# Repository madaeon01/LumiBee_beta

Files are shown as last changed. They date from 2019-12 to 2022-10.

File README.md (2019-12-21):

# LumiBee_beta

This is a WIP project.
Here you can find:
-all the 3d printable parts as STL;
-all the non 3d printable parts;
-the PCB eagle files;
-the arduino firmware;
-the chitubox profiles;
-the Android APP beta. Note: the current app stores the PNGs in the app directly, so you must put all your layers in the
RES\drawables folder manually, then compile. I plan to implement the ability to select files from a folder 
from the App, but at the moment, all the LumiBee development (hardware, software, firmware, app and all the testing) is done by 
ONE single person (me) as a side project, for free. So feel free to contribute.

To do:
-complete BOM
-assembly instructions
-how to use the screen luminosity tester
-how to use - guide
-how to use the app
In the next days this guide wil be update so if you do not find some info, just write me.

A 3D viewable model of the assembly is available here:
https://sketchfab.com/3d-models/lumibee-43fde758bdf04565baee1a75a64f292f

You can contribute to this project with a donation to support it if you like it, with a paypal donation at madaeon@gmail.com

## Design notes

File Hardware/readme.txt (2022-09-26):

List of hardware components.
Update: added latest STEP cad files.

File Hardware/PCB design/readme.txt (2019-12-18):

This is the last revision of the PCB design.

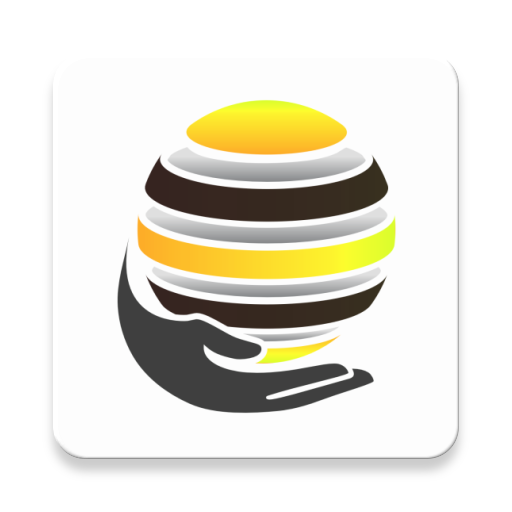
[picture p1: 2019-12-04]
app/src/main/ic_launcher-web.png

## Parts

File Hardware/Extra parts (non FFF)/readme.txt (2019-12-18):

Here you can find the parts that are not 3d printable.

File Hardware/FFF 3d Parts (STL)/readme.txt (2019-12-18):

Here you can find all the FFF printable files.

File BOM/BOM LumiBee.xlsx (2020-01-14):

Group | Part name | Printing order | Quantity | Infill | Material | Notes | Cost | Supplier
FFM Printed parts - black | LumiBee Segment A | plate 1 black | 1 | 30-40% | FDM Pla/Abs |  | n.d.
 | LumiBee Segment C | plate 1 black | 1 | 30-40% | FDM Pla/Abs |  | n.d.
 | LumiBee RoundFit conn | plate 1 black | 2+1 | 30-40% | FDM Pla/Abs |  | n.d.
 | LumiBee Segment E | plate 1 black | 1 | 30-40% | FDM Pla/Abs |  | n.d.
 | LumiBee tray PtA | plate 1 black | 1 | 70% ++ | FDM Pla/Abs |  | n.d.
 | LumiBee PostButton | plate 1 black | 3+1 | 30-40% | FDM Pla/Abs |  | n.d.
FFM Printed parts - yellow | LumiBee Segment B | plate 2 yellow | 1 | 30-40% | FDM Pla/Abs |  | n.d.
 | LumiBee Segment F | plate 2 yellow | 1 | 30-40% | FDM Pla/Abs |  | n.d.
 | LumiBee SnapFit conn | plate 2 yellow | 3+1 | 30-40% | FDM Pla/Abs |  | n.d.
 | LumiBee Round conn | plate 2 yellow | 2+1 | 30-40% | FDM Pla/Abs |  | n.d.
 | LumiBee Segment D | plate 2 yellow | 4 | 30-40% | FDM Pla/Abs |  | n.d.
 | LumiBee Leadscrew | plate 2 yellow | 2 | 70% ++ | FDM Pla/Abs |  | n.d.
 | LumiBee tray PtB | plate 2 yellow | 1 | 70% ++ | FDM Pla/Abs |  | n.d.
 | LumiBee Segment F Top Lid | plate 2 yellow | 1 | 30-40% | FDM Pla/Abs |  | n.d.
Hard plastic parts | Resin_Container |  | 1 |  | Resin 3d Printed | Can be machined from 14mm plexi too | n.d.
Neoprene parts | Neoprene-Border |  | 1 |  | Rigid 2mm Neoprene |  | n.d.
Aluminum laser cut parts | bottom-vat |  | 1 |  | Aluminium 4mm | CNC cut | n.d.
 | LumiBee Tray ALU plate |  | 1 |  | Aluminium 4mm | CNC cut | n.d.
Hardware | countersunk screw m3x6mm |  | 22 |  |  | 8 for bottom vat
 |  |  |  |  |  | 6 for LumiBee SnapFit conn
 |  |  |  |  |  | 4 for LumiBee Round conn
 |  |  |  |  |  | 4 for attaching vat to segment B
 |  |  |  |  |  | 4 for stepper motors
 | countersunk screw m3x8mm |  | 8 |  |  | 4 for alu plate
 |  |  |  |  |  | 4 for tray pt B
 | countersunk screw m3x16mm |  | 8 |  |  | 4 rear conn segment C
 |  |  |  |  |  | 4 attach segment C to parts of D
 | threaded insert M3x4mm |  | 12 |  |  | 4 for vat
 |  |  |  |  |  | 8 for segment D parts
 |  |  |  |  |  | 2 for top pcb on segment E
 | m3x8 screw |  | 4 |  |  | for endstops
 | m3x40 screw |  | 4 |  |  | for segment F
 | countersunk screw m3x13mm |  | 4 |  |  | for top fan
 | 4 m2x14 screws + nut |  | 4 |  |  | to hold leadscrews
 | Lm4uu linear bearing |  | 2
 | Linear shaft dia 4mm L=95mm |  | 2
 | Spacer nylon black M3 L=20mm |  | 4
Electronic components | Optical endstop |  | 2 |  |  | the led of the endstop must be removed and/or mounted on the other side of the pcb
 | Fan 12V 40x40x10mm |  | 1
 | Motech stepper 14 HR 05 |  | 2
 | LumiBee DC jack |  | 1
 | LumiBee PCB board |  | 1
 | stepstick 2130 |  | 2
 | arduino micro |  | 1
Plexiglass parts | LumiBee Side Plexi window |  | 2 |  | trasparent red plexiglass 3mm | Product name: "Metacrilato ACRIDITE 320 Rosso 1" |  | www.Plexishop.it
 | LumiBee Door Plexi |  | 2 |  | trasparent red plexiglass 3mm | Product name: "Metacrilato ACRIDITE 320 Rosso 1"
 | LumiBee Frame Plexi window |  | 2 |  | trasparent red plexiglass 3mm | Product name: "Metacrilato ACRIDITE 320 Rosso 1"
Magnets | Neodimium Cube 4x4x4mm |  | 8 |  |  |  |  | https://www.supermagnete.it/
 | Neodimium 5 x 2,5 x 2 mm Q-05-2.5-02-HN |  | 8

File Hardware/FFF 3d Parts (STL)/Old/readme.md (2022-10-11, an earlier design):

These parts are from a previous version, created in 2019 or earlier.

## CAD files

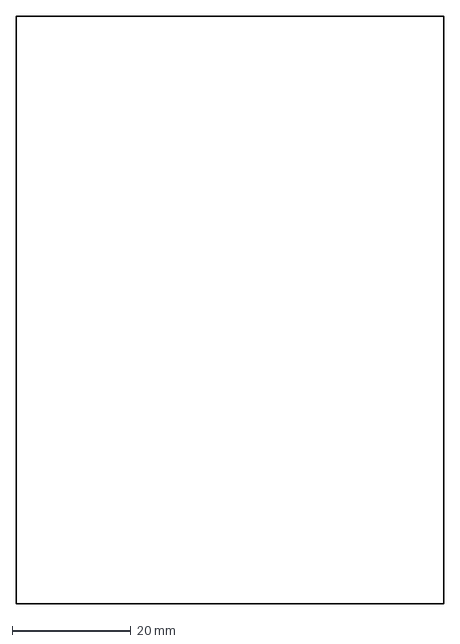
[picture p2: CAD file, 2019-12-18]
Hardware/Extra parts (non FFF)/LumiBee Side Plexi window.DXF
72.0 x 99.0 mm

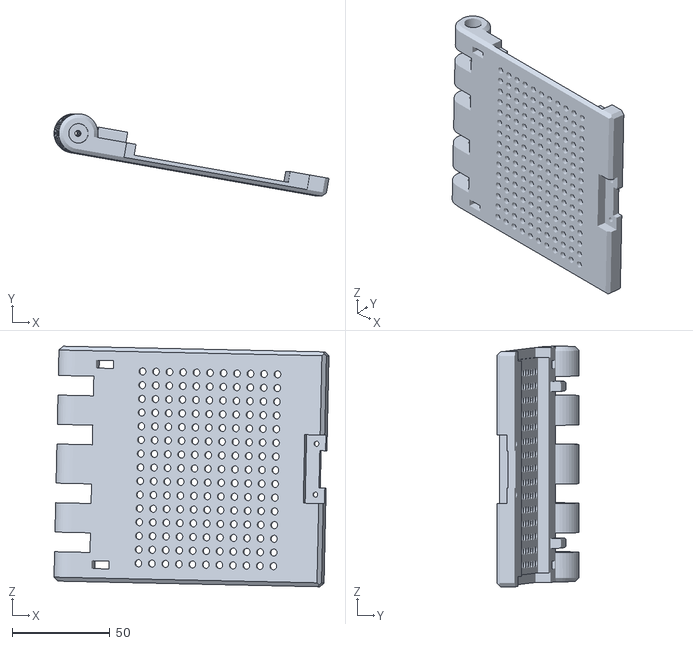
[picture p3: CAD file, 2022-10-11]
Hardware/FFF 3d Parts (STL)/LumiBee Segment A.STL
140.4 x 42.1 x 122.9

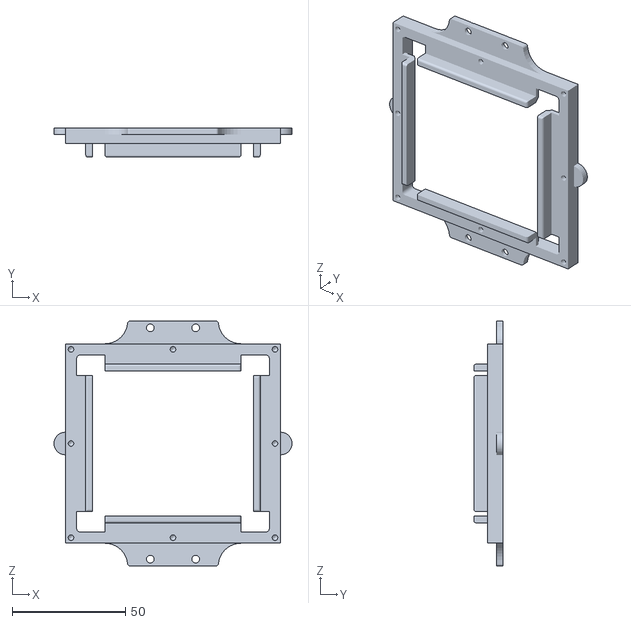
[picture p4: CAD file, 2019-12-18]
Hardware/Extra parts (non FFF)/Resin_Container.STL
105.0 x 13.0 x 108.0

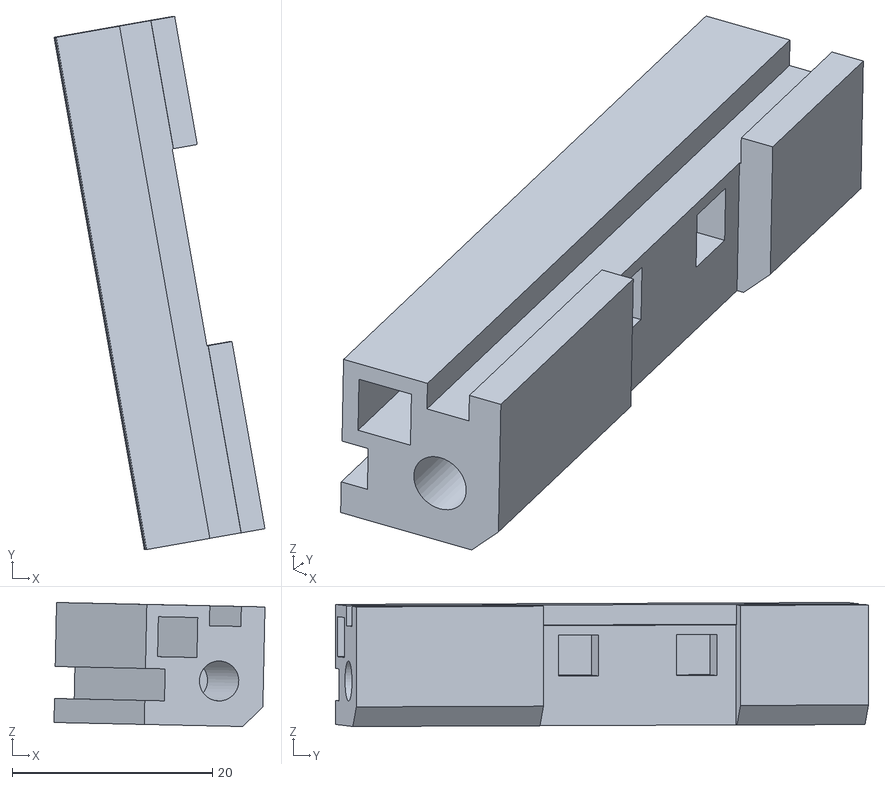
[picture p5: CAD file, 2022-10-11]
Hardware/FFF 3d Parts (STL)/LumiBee Segment D (y).STL
21.1 x 53.3 x 12.4

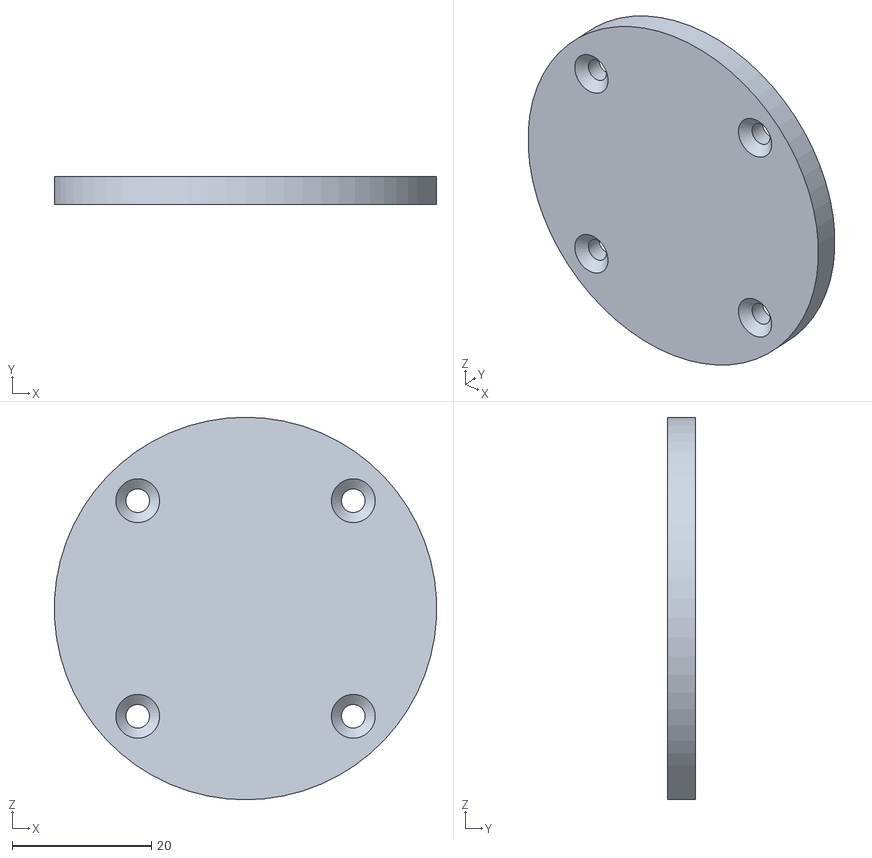
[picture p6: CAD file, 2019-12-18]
Hardware/Extra parts (non FFF)/LumiBee Tray ALU plate.STL
54.9 x 4.00 x 55.0

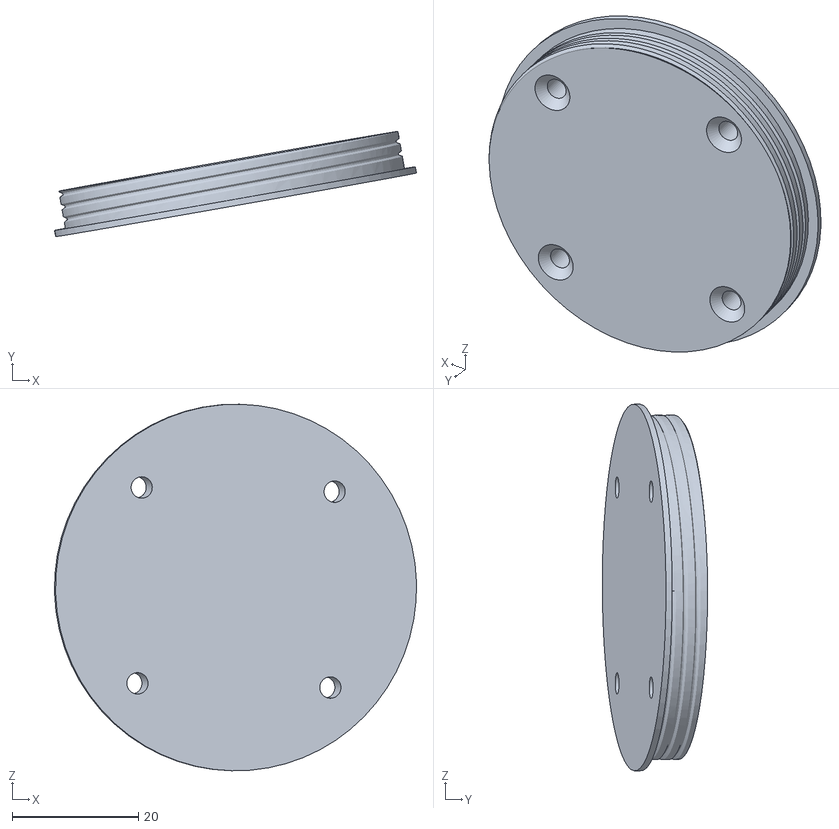
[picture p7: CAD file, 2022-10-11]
Hardware/FFF 3d Parts (STL)/LumiBee Tray ptB (y).STL
57.3 x 16.7 x 58.0

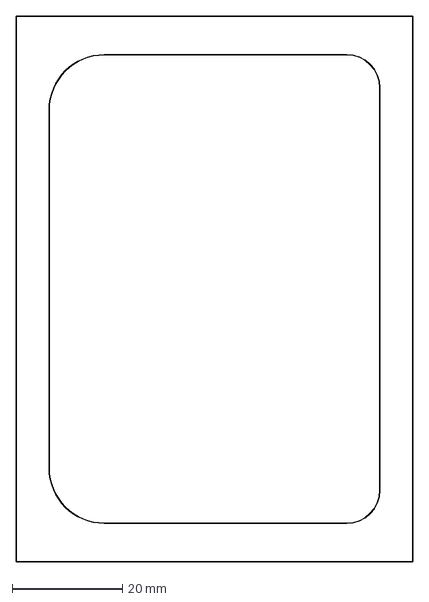
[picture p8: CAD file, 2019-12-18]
Hardware/Extra parts (non FFF)/LumiBee Frame Plexi window.DXF
72.0 x 99.0 mm

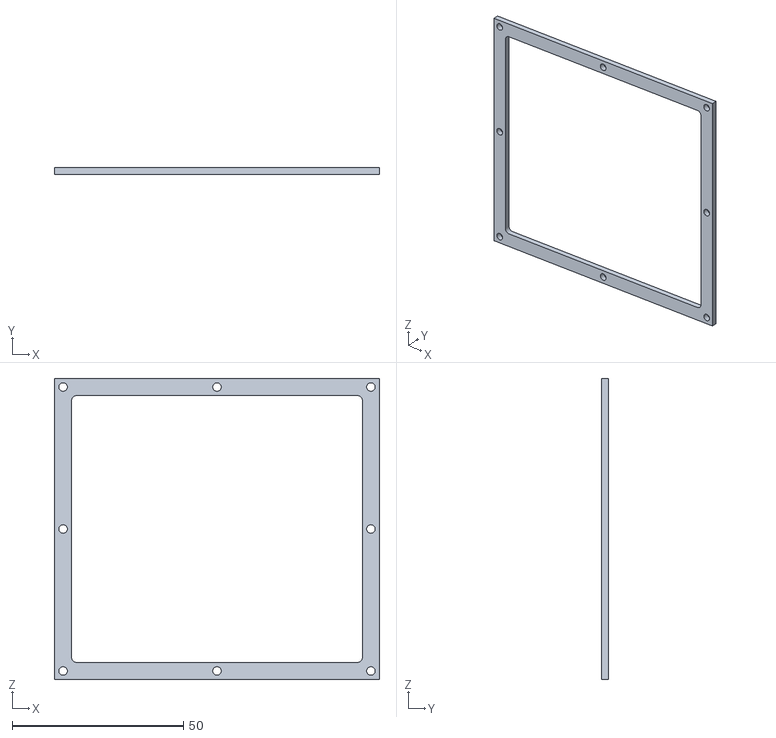
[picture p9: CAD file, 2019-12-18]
Hardware/Extra parts (non FFF)/Neoprene-Border.STL
95.0 x 2.00 x 88.0

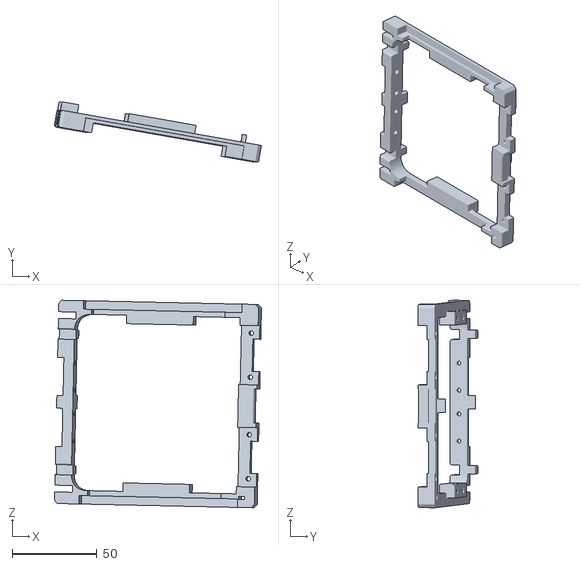
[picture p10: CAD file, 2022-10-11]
Hardware/FFF 3d Parts (STL)/LumiBee Segment B (y).STL
122.2 x 35.6 x 122.5

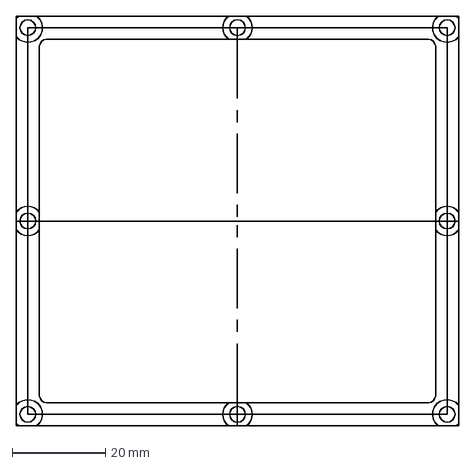
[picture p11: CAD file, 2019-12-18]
Hardware/Extra parts (non FFF)/BottomVat.DXF
95.0 x 88.0 mm

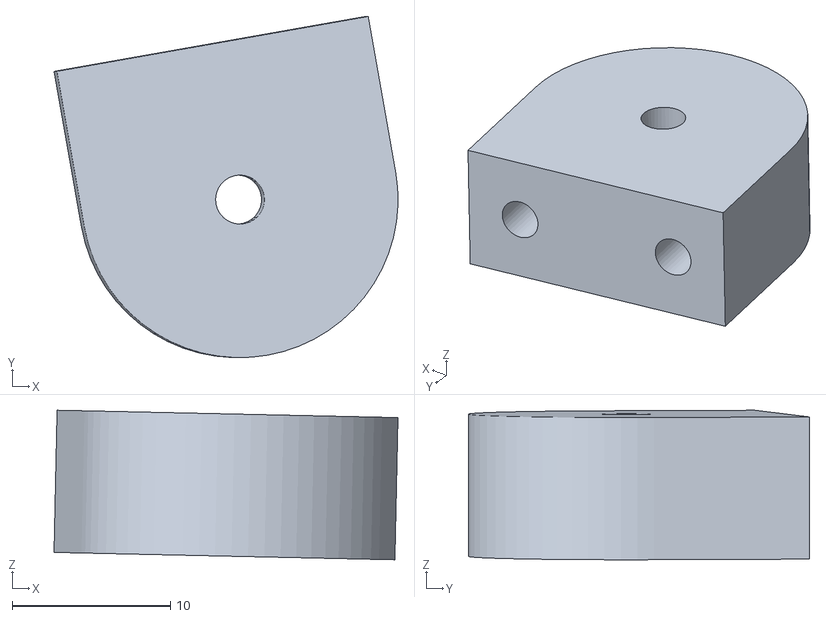
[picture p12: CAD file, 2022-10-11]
Hardware/FFF 3d Parts (STL)/LumiBee RoundFit conn.STL
21.8 x 21.6 x 9.46

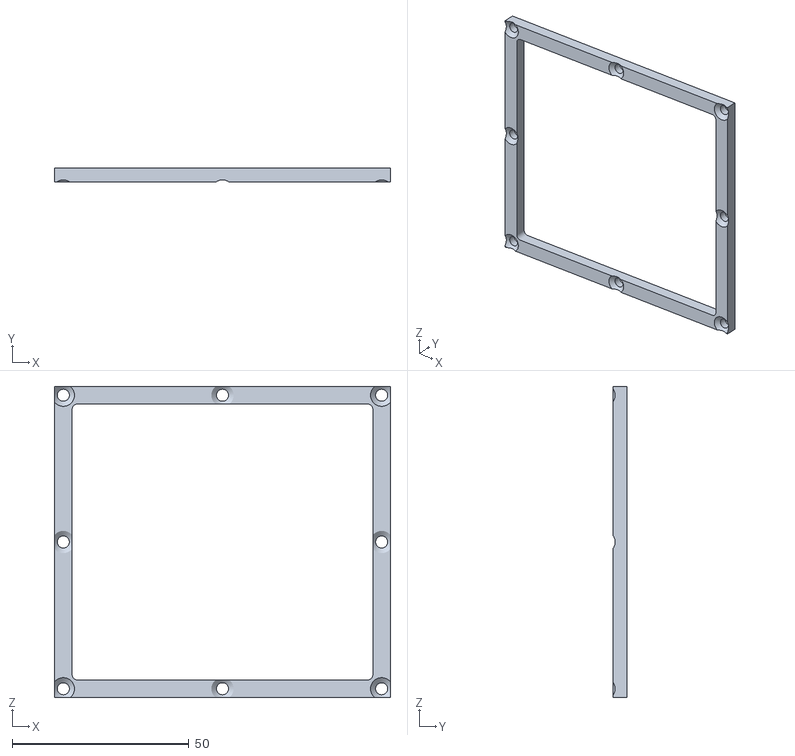
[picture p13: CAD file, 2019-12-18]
Hardware/Extra parts (non FFF)/ALU - BottomVat.STL
95.0 x 4.00 x 88.0

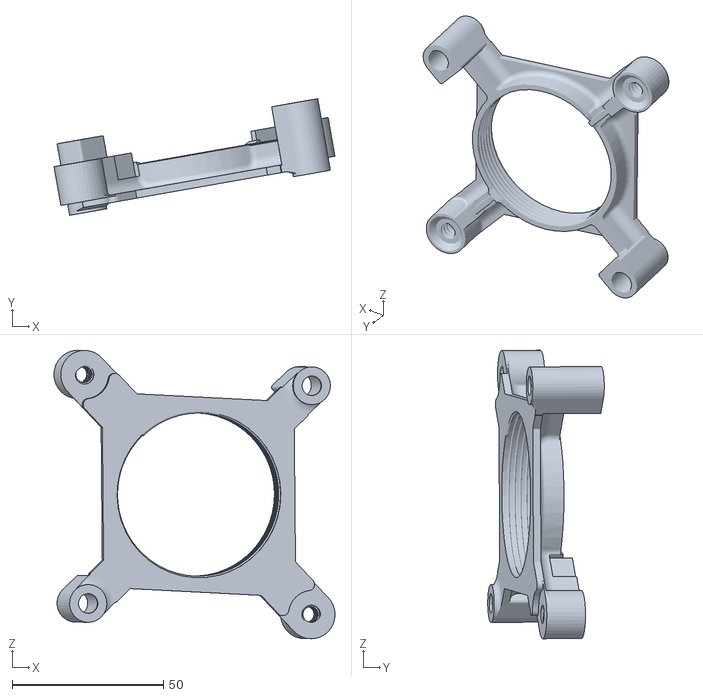
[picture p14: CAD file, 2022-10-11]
Hardware/FFF 3d Parts (STL)/LumiBee tray ptA.STL
92.9 x 38.6 x 95.4

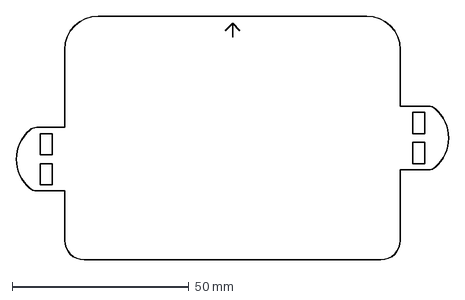
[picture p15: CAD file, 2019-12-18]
Hardware/Extra parts (non FFF)/LumiBee Door Plexi.DXF
122.4 x 69.0 mm

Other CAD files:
Hardware/FFF 3d Parts (STL)/LumiBee Segment C.STL
Hardware/FFF 3d Parts (STL)/LumiBee SnapFit conn (y).STL
Hardware/FFF 3d Parts (STL)/LumiBee PostButton.STL
Hardware/FFF 3d Parts (STL)/LumiBee Round conn (y).STL
Hardware/Extra parts (non FFF)/LumiBee Tray ALU plate.DXF
Hardware/Extra parts (non FFF)/Neoprene-Border.DXF
Hardware/FFF 3d Parts (STL)/LumiBee Segment E.STL
Hardware/FFF 3d Parts (STL)/LumiBee Segment F (y).STL
Hardware/FFF 3d Parts (STL)/LumiBee Segment F Top Lid (y).STL
Hardware/FFF 3d Parts (STL)/LumiBee leadscrew (y).STL
Hardware/FFF 3d Parts (STL)/Old/LumiBee PostButton.STL
Hardware/FFF 3d Parts (STL)/Old/LumiBee Round conn (y).STL
Hardware/FFF 3d Parts (STL)/Old/LumiBee RoundFit conn.STL
Hardware/FFF 3d Parts (STL)/Old/LumiBee Segment A.STL
Hardware/FFF 3d Parts (STL)/Old/LumiBee Segment B (y).STL
Hardware/FFF 3d Parts (STL)/Old/LumiBee Segment C.STL
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

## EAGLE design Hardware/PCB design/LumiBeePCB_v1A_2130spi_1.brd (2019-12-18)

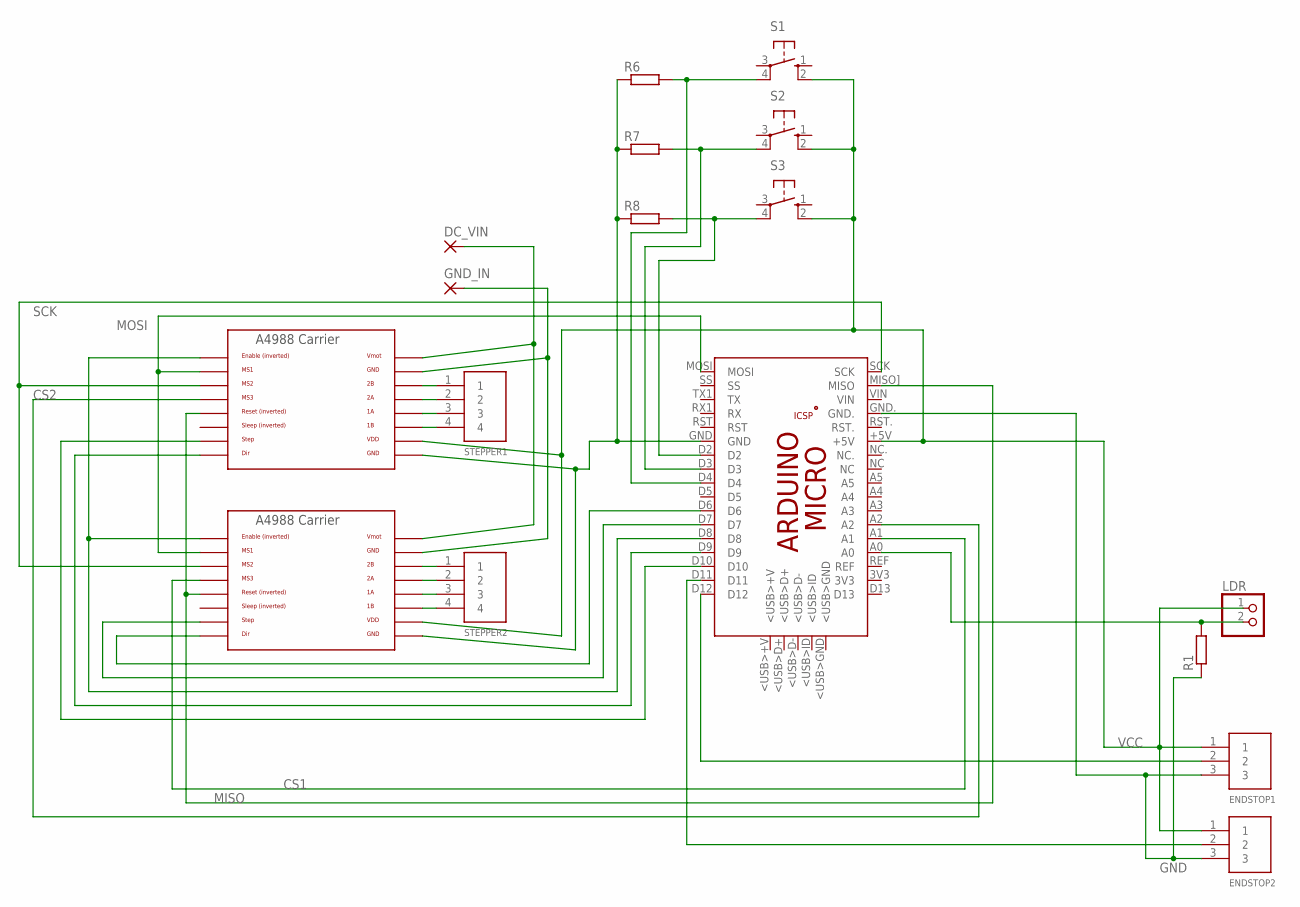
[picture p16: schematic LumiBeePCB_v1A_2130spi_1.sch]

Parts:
DC_VIN: 2,54/0,8
ENDSTOP1, ENDSTOP2: 3PIN; B3B-PH-K-S
GND_IN: 2,54/0,8
LDR: PINHD-1X2; 1X02
PCB1: ARDUINO_MICRO
R1, R6, R7, R8: R-EU_M1206; M1206
S1, S2, S3: 10-XX; B3F-10XX
STEPPER1, STEPPER2: 4PIN; B4B-PH-K-S
U$1, U$2: A4988BREAKOUT

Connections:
CS1: PCB1.A1, U$2.MS3
CS2: PCB1.A2, U$1.MS3
GND: ENDSTOP1.3, ENDSTOP2.3, PCB1.GND., R1.1
MISO: PCB1.MISO] (MISO), U$1.RST, U$2.RST
MOSI: PCB1.MOSI, U$1.MS1, U$2.MS1
unnamed: GND_IN.1, U$1.GND, U$2.GND
unnamed: DC_VIN.1, U$1.VMOT, U$2.VMOT
unnamed: STEPPER1.1, U$1.2B
unnamed: PCB1.GND, R6.1, R7.1, R8.1, U$1.GND@0 (GND), U$2.GND@0 (GND)
unnamed: ENDSTOP1.2, PCB1.D12
unnamed: STEPPER1.2, U$1.2A
unnamed: STEPPER1.3, U$1.1A
unnamed: STEPPER1.4, U$1.1B
unnamed: STEPPER2.1, U$2.2B
unnamed: STEPPER2.2, U$2.2A
unnamed: STEPPER2.3, U$2.1A
unnamed: STEPPER2.4, U$2.1B
unnamed: ENDSTOP2.2, PCB1.D11
unnamed: PCB1.D10, U$1.STEP
unnamed: PCB1.D9, U$1.DIR
unnamed: PCB1.D8, U$1.EN, U$2.EN
unnamed: PCB1.D7, U$2.STEP
unnamed: PCB1.D6, U$2.DIR
unnamed: LDR.2, PCB1.A0, R1.2
unnamed: PCB1.D2, R8.2, S3.4 (P1)
unnamed: PCB1.D3, R7.2, S2.4 (P1)
unnamed: PCB1.D4, R6.2, S1.4 (P1)
SCK: PCB1.SCK, U$1.MS2, U$2.MS2
VCC: ENDSTOP1.1, ENDSTOP2.1, LDR.1, PCB1.+5V, S1.2 (S1), S2.2 (S1), S3.2 (S1), U$1.VDD, U$2.VDD

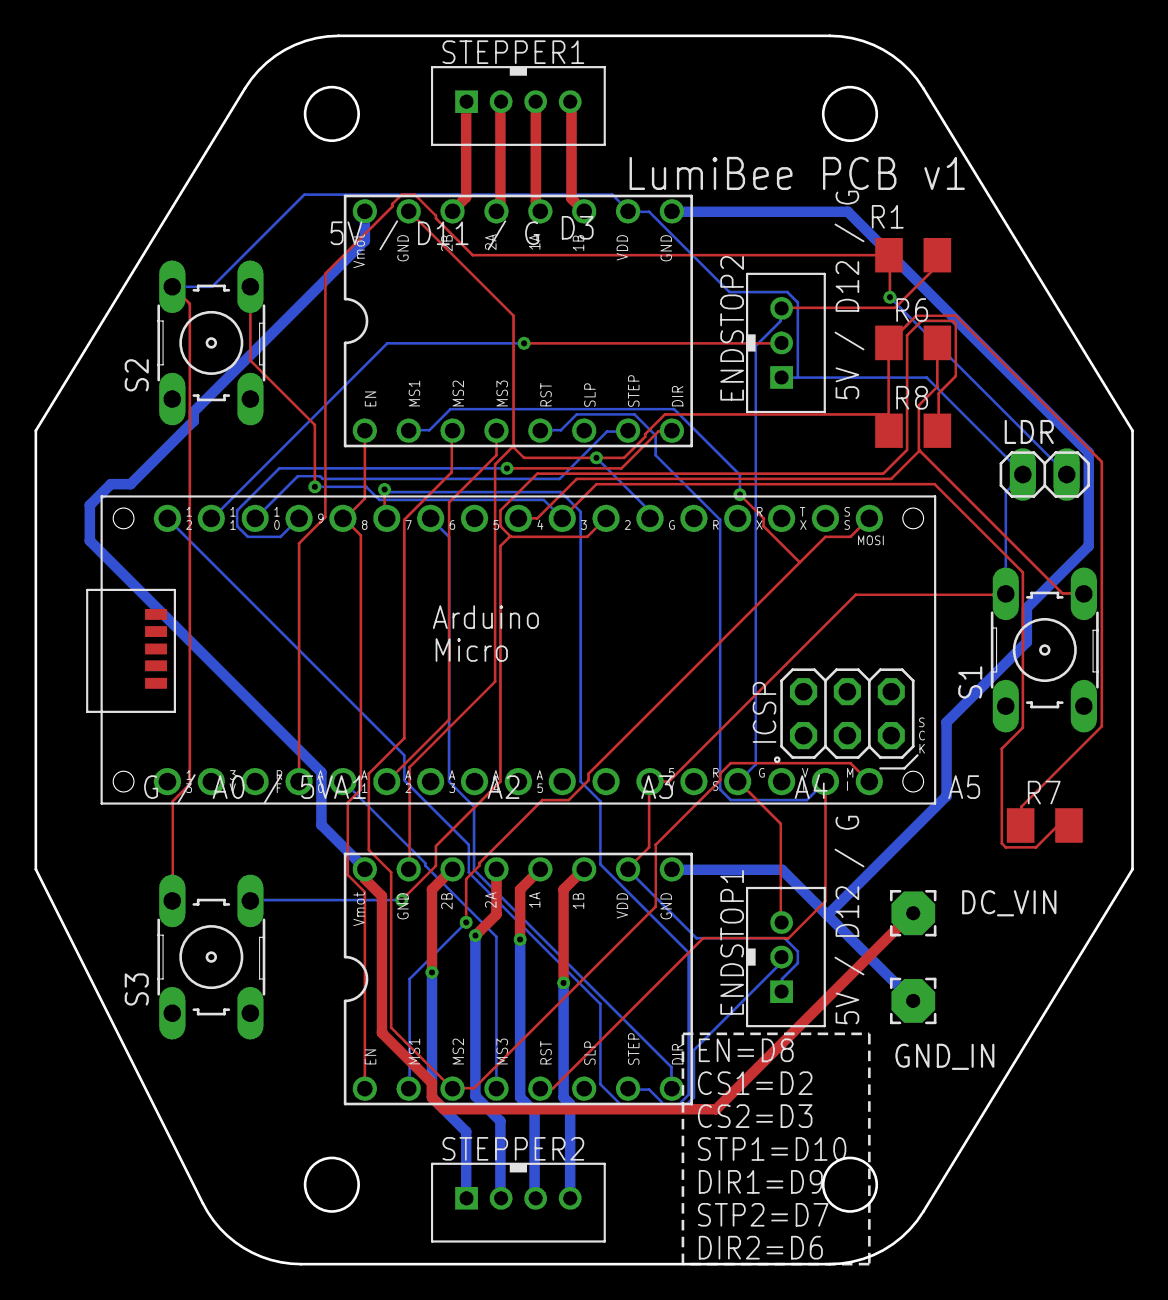
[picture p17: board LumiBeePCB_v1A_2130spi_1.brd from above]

Board: 2 copper layers, 63.5 x 71.1 mm, 17 parts (0 on the bottom side), 29 nets.

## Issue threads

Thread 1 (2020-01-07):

Additional information needed

naldarn, 2020-01-07:
In preparing to build the LumiBee, looking at the parts Resin_Container.STL, BottomVat.DXF, they do not list a material on the filename like the other files.

madaeon01, 2020-01-08:
thanks, will fix this tomorrow.

madaeon01, 2020-01-09:
I have updated the BOM file.
Resin_Container -> this holds the resin, so I recommend NOT to print it with FFF, or it will be damaged soon by the resin. I used our resin 3D Printer to make this part. You can also machine it from 14mm plexiglass, but it would be more expensive.
AluPlate and BottomVat is 4mm aluminum CNC cut.
NeopreneBorder, is 2mm hard neoprene CNC or laser cut.

Closed 2020-01-20.

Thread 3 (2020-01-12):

How to contain resin

taylorzane, 2020-01-12:
I understand most of this build, but one thing I'm having trouble following is how the resin is held in the vat. The parts for the vat don't seem to have a bottom/sides to prevent the resin from flowing onto the phone/work surface. Are you using some sort of plastic wrap sandwiched between the vat pieces?

Thanks!

taylorzane, 2020-01-12:
Another question would be what type of acrylic would you recommend for the windows? They appear to be dark red, but I imagine they're a little more specialized than that.

madaeon01, 2020-01-14:
Hi, added info in https://github.com/madaeon01/LumiBee_beta/wiki/The-resin-VAT
Updated also BOM with plexiglass supplier and type.

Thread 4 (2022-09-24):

BOM Missing Something

MxRemy, 2022-09-24:
There doesn't seem to be anything listed in the BOM to hold segment A and the various round connectors together. The longest part listed in the BOM is the m3x40 screws, and even those aren't half as long as they'd need to be to reach all the way across segment A:
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
Also, the fully assembled 3d model that you link to shows an entirely different design for this part of segment A:
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
You probably ideally wouldn't use a screw for this anyway right? Since it's meant to pivot smoothly?

madaeon01, 2022-09-26:
These are the most updated files:
https://3dsolutions.store/PF_files/LumiBee%20with%20plexi%20Expo%20box.STEP
WIth this model, 40mm screw is fine. Or you can use the Segment A you already printed and longer screws.

MxRemy, 2022-10-11:
The latest version of the files have now been uploaded as STLs, as you said they solve this issue. Although I think it works better with a single long rod that's only threaded at the ends.

Closed 2022-10-11.

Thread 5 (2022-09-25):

Segment C socket for Leadscrew is too tight.

MxRemy, 2022-09-25:
I think the leadscrew is supposed to turn freely in this socket, it wouldn't work otherwise, but it's too tight. I couldn't even get it back out and ended up snapping it off in the process:
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
This was in a pretty sturdy PLA at 100% infill and good settings for end-use parts. Should have been well within tolerances. I also couldn't get the broken piece out, and rather than reprint Segment C, I used heated rods to bore out the hole again. I have no idea if it will work or if I'll need to reprint that piece too. If there's no particular reason these sockets need to be so snug, I think they should be made way looser.

madaeon01, 2022-09-26:
Hi.
I printed mine with a Zortrax M200. It has to rotate freely.
See video: https://photos.app.goo.gl/iVsr9nTPy4gZSWVJ9

I am sharing here the Solidworks Cad file of the leadscrew, you can open it and adjust the tolerances (increase the swept cut size) to be able to print it correctly with your 3d printer.
https://3dsolutions.store/PF_files/LumiBee%20leadscrew.SLDPRT

I am sharing here also the updated Step file of the whole assembly.
https://3dsolutions.store/PF_files/LumiBee%20with%20plexi%20Expo%20box.STEP

MxRemy, 2022-10-11:
Thanks! I'll get on adjusting this when I get a chance.

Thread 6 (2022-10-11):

Snapfit won't Snap

MxRemy, 2022-10-11:
Segment A won't snap closed closed on Segment B. The part shown in the red box::
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

I think it's because my countersunk screws (in the blue circles) won't actually sit flush against the snapfit connectors. As evidence of this, Segment B has no trouble snapping closed on Segment C...

Actually, all the countersunk screws protrude a little bit, from every part that uses them. I think the inset area needs to be a teeny bit bigger? Or else it might just be my screws, they were cheap. Not sure how variable the countersinking is on screws.

madaeon01, 2022-10-12:
You can simply use a cutter, place it at an angle, and do a couple of rotations to increase the countersunk area.

MxRemy, 2022-10-12:
Good call! I'll do that, but when I get a chance, should I try and make the countersunk area deeper/wider in the file itself? Or do you think this is just happening with my copies?

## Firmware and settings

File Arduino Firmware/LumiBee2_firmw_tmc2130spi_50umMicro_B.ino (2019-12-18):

//**************************************************************************************
//* Funzione dei pulsanti
/// btnS1 Bottone frontale singolo (pin 4)   btn1 , endstop
/// btnS2 Bottone dietro sinistra (pin 2)    btn2 , UP both
/// btnS3 Bottone dietro destra (pin 3)      btn3 , DW both
//*
//**************************************************************************************


//#include <SPI.h>
#include <Trinamic_TMC2130.h>
#include <elapsedMillis.h>

// pin configuration

#define CS_PIN1 A1   //19  //A1
#define z1step 7
#define z1dir 6

#define CS_PIN2 A2         //20  //A2
#define z2step 10
#define z2dir 9
#define steppersEnable 8

#define z1Endstop 11
#define z2Endstop 12

#define ldrPin A0

#define btnS1 4   
#define btnS2 3
#define btnS3 2

//#define ledR 3
//#define ledG 5
//#define ledB 6

Trinamic_TMC2130 myStepper2(CS_PIN1);
Trinamic_TMC2130 myStepper1(CS_PIN2);

#define nMicrosteps 2

// Movimenti singoli motore 1
//----------------------------------------------------------------------
void stepDW1(int steps)
{  digitalWrite(z1dir, LOW); 
   for(int a=0; a<steps; a++) {//if (digitalRead(zMinSensor))
   { digitalWrite(z1step, HIGH);   
     delayMicroseconds(150);               
     digitalWrite(z1step, LOW); 
     delayMicroseconds(900);
     }}
}  

void stepUP1(int steps)
{  digitalWrite(z1dir, HIGH); 
   for(int a=0; a<steps; a++) {//if (digitalRead(zMinSensor))
   { digitalWrite(z1step, HIGH);   
     delayMicroseconds(150);               
     digitalWrite(z1step, LOW); 
     delayMicroseconds(900);
     }}
}  

// Movimenti singoli motore 2
//----------------------------------------------------------------------
void stepDW2(int steps)
{  digitalWrite(z2dir, LOW); 
   for(int a=0; a<steps; a++) {//if (digitalRead(zMinSensor))
   { digitalWrite(z2step, HIGH);   
     delayMicroseconds(150);               
     digitalWrite(z2step, LOW); 
     delayMicroseconds(900);
     }}
}  

void stepUP2(int steps)
{  digitalWrite(z2dir, HIGH); 
   for(int a=0; a<steps; a++) {//if (digitalRead(zMinSensor))
   { digitalWrite(z2step, HIGH);   
     delayMicroseconds(150);               
     digitalWrite(z2step, LOW); 
     delayMicroseconds(900);
     }}
   }  

// Movimenti combinati motore 1 e 2 insieme
//----------------------------------------------------------------------
void stepDWboth(int steps)
{  digitalWrite(z2dir, HIGH); 
   digitalWrite(z1dir, HIGH); 
   for(int a=0; a<steps; a++) {//if (digitalRead(zMinSensor))
   { digitalWrite(z1step, HIGH);   digitalWrite(z2step, HIGH);   
     delayMicroseconds(150);               
     digitalWrite(z1step, LOW); digitalWrite(z2step, LOW); 
     delayMicroseconds(900);
     }}
}  

void stepUPboth(int steps)
{  digitalWrite(z2dir, LOW); 
   digitalWrite(z1dir, LOW); 
   for(int a=0; a<steps; a++) 
   { if ( (digitalRead(z1Endstop)==LOW) && (digitalRead(z2Endstop)==LOW) )
     { digitalWrite(z1step, HIGH);   digitalWrite(z2step, HIGH);   
     delayMicroseconds(150);               
     digitalWrite(z1step, LOW); digitalWrite(z2step, LOW); 
     delayMicroseconds(900);
     }
   }
}  



void stepToEndstop()
{  digitalWrite(z2dir, LOW); 
   digitalWrite(z1dir, LOW); 
   // Prima insieme
   while ( (digitalRead(z1Endstop)==LOW) && (digitalRead(z2Endstop)==LOW) )
   { digitalWrite(z1step, HIGH);   digitalWrite(z2step, HIGH);   
     delayMicroseconds(150);               
     digitalWrite(z1step, LOW); digitalWrite(z2step, LOW); 
     delayMicroseconds(900);
     }  delay(500); 
// Poi livella singolarmente: motore 1
   while (digitalRead(z1Endstop)==LOW)
   { digitalWrite(z1step, HIGH);     delayMicroseconds(150);               
     digitalWrite(z1step, LOW);      delayMicroseconds(900);
     }  delay(500);        
//Poi livella singolarmente: motore 2
   while (digitalRead(z2Endstop)==LOW)
   { digitalWrite(z2step, HIGH);     delayMicroseconds(150);               
     digitalWrite(z2step, LOW);      delayMicroseconds(900);
     }   delay(500);     
// colpetto finale a entrambi di 1mm su
   digitalWrite(z2dir, LOW); 
   digitalWrite(z1dir, LOW); 
   for(int a=0; a<200; a++) 
   { digitalWrite(z1step, HIGH);   digitalWrite(z2step, HIGH);   
     delayMicroseconds(150);               
     digitalWrite(z1step, LOW); digitalWrite(z2step, LOW); 
     delayMicroseconds(900);
    } 

    
} 

void stepToEndstopEgo()
{  stepToEndstop();
// ora giu' pronto a stampare
  stepDWboth(16250);
    
}  
   

// Funzioni di stampa 3d
//----------------------------------------------------------------------

// passo elica leadscrew 3d printed:  2 mm = 1 giro
// stepper da 0.9° = 400 step / giro
// con microstep a 2,  800 step per fare 2mm
//                     80 step per fare 0.2mm
//                     40 step per 0.1mm

void zLayerUp() // su di 1 layer con stacco, stampa a 100um
{ //  su di 10 (ex 5) mm
  stepUPboth(4000);
  delay(500); 
  //// giù di 4mm meno 0.1mm
  // giù di 4mm meno 0.05mm
  stepDWboth(4000-20);             
}  


void zLayerUpShort() // su di 1 layer con stacco, stampa a 100um
{ //  su di 10 (ex 5) mm
  stepUPboth(1000);
  delay(200); 
  //// giù di 4mm meno 0.1mm
  // giù di 4mm meno 0.05mm
  stepDWboth(1000-20);             
}  


void blinks(int times)
{ for (int i=0; i<times; i++)
  { digitalWrite(13, HIGH);
    delay(150); 
   digitalWrite(13, LOW);
    delay(150);
  }
}

void setup() {
    // inizializzazione stepper motors per pompa e asse Z


 pinMode(CS_PIN1, OUTPUT);
 pinMode(CS_PIN2, OUTPUT); 

  pinMode(13, OUTPUT); 
 
   pinMode(z1step, OUTPUT);
   pinMode(z1dir, OUTPUT);      
   pinMode(z2step, OUTPUT);
   pinMode(z2dir, OUTPUT);      
 pinMode(steppersEnable, OUTPUT); 

   pinMode(z1Endstop, INPUT);      
   pinMode(z2Endstop, INPUT);         
    
   pinMode(btnS1, INPUT);     
   pinMode(btnS1, INPUT); 
   pinMode(btnS3, INPUT);   

     digitalWrite(steppersEnable, LOW); 

 // stepper 1
  myStepper1.init();
  myStepper1.set_mres(nMicrosteps); // ({1,2,4,8,16,32,64,128,256}) number of microsteps
  myStepper1.set_IHOLD_IRUN(12,12,5); // ([0-31],[0-31],[0-5]) sets all currents to maximum
  myStepper1.set_I_scale_analog(1); // ({0,1}) 0: I_REF internal, 1: sets I_REF to AIN
  myStepper1.set_tbl(1); // ([0-3]) set comparator blank time to 16, 24, 36 or 54 clocks, 1 or 2 is recommended
  myStepper1.set_toff(8); // ([0-15]) 0: driver disable, 1: use only with TBL>2, 2-15: off time setting during slow decay phase

// stepper 2
  myStepper2.init();
  myStepper2.set_mres(nMicrosteps); // ({1,2,4,8,16,32,64,128,256}) number of microsteps
  myStepper2.set_IHOLD_IRUN(12,12,5); // ([0-31],[0-31],[0-5]) sets all currents to maximum
  myStepper2.set_I_scale_analog(1); // ({0,1}) 0: I_REF internal, 1: sets I_REF to AIN
  myStepper2.set_tbl(1); // ([0-3]) set comparator blank time to 16, 24, 36 or 54 clocks, 1 or 2 is recommended
  myStepper2.set_toff(8); // ([0-15]) 0: driver disable, 1: use only with TBL>2, 2-15: off time setting during slow decay phase  
       

//stepDW1(200);
//stepDW2(200);
//stepUP1(200);
//stepUP2(200);

   
    Serial.begin(9600);    
    
}

void loop() {
   // per dubug mode
   int incomingByte = 0; // for incoming serial data
   if (Serial.available() > 0)
     { incomingByte = Serial.read();
         if (incomingByte=='a') // test layer 50um
          { for (int k=0; k<50; k++) zLayerUpShort(); } // 0.05 x 50 = 2.5mm
     }


 // Serial.println(analogRead(ldrPin));

  elapsedMillis timeElapsed;
  boolean isoff=false;
  boolean isfin=false;
  if (analogRead(ldrPin)>850)
  { 
    
    /////delay(250);
    timeElapsed = 0;  
    do 
    { if (analogRead(ldrPin)<300) isoff=true;
      if ((isoff==true)&&(analogRead(ldrPin)>850)) { isfin=true; stepToEndstop(); blinks(2); }
    } while (timeElapsed < 300);
    
    if (isfin==false) { zLayerUp();  blinks(4); }


    
  }

   if (digitalRead(z1Endstop)==HIGH) {Serial.println("Endstop 1 high"); delay(50);}// else {Serial.println("Endsotp low"); delay(50);}
   if (digitalRead(z2Endstop)==HIGH) {Serial.println("Endstop 2 high"); delay(50);}// else {Serial.println("Endsotp low"); delay(50);}   
   if (digitalRead(btnS2)==HIGH) {blinks(1);  Serial.println("btns2 , UP both"); delay(150); stepUPboth(200); } //else {Serial.println("btn1 low"); delay(50);}
   if (digitalRead(btnS3)==HIGH) {blinks(2); Serial.println("btns3 , DW both"); delay(150); stepDWboth(200); } //
   if (digitalRead(btnS1)==HIGH) {blinks(3); Serial.println("btns1 to endstop"); delay(150); Serial.println(analogRead(ldrPin)); stepToEndstopEgo(); } //   

   
}

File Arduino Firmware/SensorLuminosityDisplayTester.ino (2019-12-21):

/* Photocell simple testing sketch. 
 
Connect one end of the photocell to 5V, the other end to Analog 0.
Then connect one end of a 10K resistor from Analog 0 to ground 
Connect LED from pin 11 through a resistor to ground 
For more information see http://learn.adafruit.com/photocells */

//#include <U8g2lib.h>
//#include <SPI.h>
//#include <Wire.h>

//#include <Adafruit_GFX.h>
#include <Adafruit_SSD1306.h>

Adafruit_SSD1306 display(4);
 
int photocellPin1 = 0;     // the cell and 10K pulldown are connected to a0
int photocellPin2 = 1;     // the cell and 10K pulldown are connected to a0
int photocellPin3 = 2;     // the cell and 10K pulldown are connected to a0

int photocellReading1;     // the analog reading from the sensor divider
int photocellReading2;     // the analog reading from the sensor divider
int photocellReading3;     // the analog reading from the sensor divider



void printLabel(boolean doClear, String txt, int value, int y)
{
  //if (doClear == true) display.clearDisplay();
  display.setCursor(0, y);
  String thisString = String(value);
  display.setTextSize(1);
  display.setTextColor(WHITE);
  display.print(thisString); Serial.print(thisString);
  display.print(txt);        Serial.println(txt);
  
}



void setup(void) {
  // We'll send debugging information via the Serial monitor
  Serial.begin(115200);   
  

  display.begin(SSD1306_SWITCHCAPVCC, 0x3C);  // initialize with the I2C addr 0x3C (for the 128x32)
  // Clear the buffer.
  display.clearDisplay();

}


 
void loop(void) {
  photocellReading1 = analogRead(photocellPin1);  
  photocellReading2 = analogRead(photocellPin2);  
  photocellReading3 = analogRead(photocellPin3);    
 
 // Serial.print("Analog reading = ");
//  Serial.print(photocellReading1); Serial.print(' ');    // the raw analog reading
//  Serial.print(photocellReading2); Serial.print(' ');    // the raw analog reading
//  Serial.println(photocellReading3);     // the raw analog reading  

//Serial.println(photocellReading1);
display.clearDisplay();
printLabel(true," lum. sens.1 ",photocellReading1,0);
printLabel(true," lum. sens.2 ",photocellReading2,10);
printLabel(true," lum. sens.3 ",photocellReading3,20);
display.display();


 /*  String str[10] = "a";//(String)photocellReading1;
   u8g2.clearBuffer();          // clear the internal memory
   u8g2.setFont(u8g2_font_logisoso28_tr);  // choose a suitable font at https://github.com/olikraus/u8g2/wiki/fntlistall
  // u8g2.drawStr(0,0,str);  // write something to the internal memory
 
 u8g2.drawStr(8,29,"MYBOTIC");  // write something to the internal memory
   u8g2.sendBuffer();         // transfer internal memory to the display
   */
//Serial.print(" ");
//Serial.println(photocellReading2);
//Serial.print(" ");
//Serial.println(photocellReading3);
//Serial.print(" ");
 
  // LED gets brighter the darker it is at the sensor
  // that means we have to -invert- the reading from 0-1023 back to 1023-0
//  photocellReading = 1023 - photocellReading;
  //now we have to map 0-1023 to 0-255 since thats the range analogWrite uses
//  LEDbrightness = map(photocellReading, 0, 1023, 0, 255);
//  analogWrite(LEDpin, LEDbrightness);
 
  delay(100);


 
}

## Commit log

2022-10-11 Putting the old files in archive
    [LumiBee PostButton.STL, LumiBee Round conn (y).STL, LumiBee RoundFit conn.STL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]
2022-10-11 Deleting old files
    [LumiBee PostButton.STL]
2022-10-11 Uploading newer files
    I exported these from the STEP file and made their names match the old ones. I'm not sure how many of them have changed from the previous version, figured it'd be safer to do all of them.
    [LumiBee PostButton.STL, LumiBee Round conn (y).STL, LumiBee RoundFit conn.STL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]
